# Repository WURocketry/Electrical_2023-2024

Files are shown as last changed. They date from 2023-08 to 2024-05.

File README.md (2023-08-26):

# Electrical
Electrical / Software Development

* Circuit CAD
* Software

### Subteam Folders
Subteams are free to modify their own folder as they like - keep all your subteam related files/articles/figures within that folder.

### Subteam Branches
The "main" Electrical repository is organized into 2 subteam development branches:

* "dev/avionics"
* "dev/payload"
* "dev/airbrakes"

Subteam changes should be pushed and pull requests made only to the respective development subteam branch!

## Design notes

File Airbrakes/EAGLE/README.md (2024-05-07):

# EAGLE IS DEPRECATED

## Use Fusion360 or alternatives

### The archived PACE was moved to the `EAGLE/` folder at the root of the 2023-2024 Electrical repo.

The team is likely using Altium and KiCad for 2025.

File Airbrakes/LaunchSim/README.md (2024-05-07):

Folder for simulation of theoretical airbrake control mechanisms including:
> * Trajectory simulator
> * VLT
> * Actuation control algorithms (PID)

A big yappin folder, courtesy of William (@wurdahl). But really important.

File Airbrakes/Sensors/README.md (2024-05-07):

Folder for sensor tests/example scripts.

Note that these kind of things should be moved to the EE repo in the future, instead of each UFS project having an isolated test area.

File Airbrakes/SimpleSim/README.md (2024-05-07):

A simple python simulation of the vehicle using motor data.

Written and yapped by Patrick (@pjkirby31)

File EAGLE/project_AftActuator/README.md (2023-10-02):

This contains EAGLE project files for the aft servo actuator board

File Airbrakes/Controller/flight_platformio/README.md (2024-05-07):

The home of airbrakes software.

## Root folder Hierarchy

### include/
This folder contains all the header files for every source file. 

A key file is the IMPORTANT_CONFIG.h file containing important configurations (go figure) of ACE software used during flight/development.

### src/
The corresponding definitions/implementations of the header files' classes

### lib/
External 3rd party libraries providing functionality

### test/
Never used. Rip. We should test code, and platformio provides a framework for that.

## Subfolder Hierarchy

### capabilities/
Contains UFS application software layer classes

### components/
Contains UFS component link layer classes

### simulation/
Files for simulating integration test data of the ACE

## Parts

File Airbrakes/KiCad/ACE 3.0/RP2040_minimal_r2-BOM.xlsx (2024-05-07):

RP2040_minimal_r2 BOM
Item | Quantity | Reference | Part | Voltage | Current | Power | Material | Size | Tolerance | Manufacturer | Manuf. Part # | Description | Notes
1 | 3 | C1,C4,C17 | 10u | 16V |  |  | X5R | 0805_2012Metric | 10% | Murata | GRM21BR61C106KE15K | CAP CER 10UF 16V X5R 0805 | Or equivalent
2 | 2 | C2, C3 | 15p | 50V |  |  | C0G | 0402_1005Metric | 5% | Murata | GCM1555C1H150JA16D | CAP CER 15PF 50V C0G/NP0 0402 | Or equivalent
3 | 10 | C5, C6, C7, C9, C11, C12, C13, C14, C15, C16 | 100n | 25V |  |  | X7R | 0402_1005Metric | 10% | Murata | GRM155R71E104KE14J | CAP CER 0.1UF 25V X7R 0402 | Or equivalent
4 | 2 | C8, C10 | 1u | 10V |  |  | X6S | 0402_1005Metric | 10% | Murata | GRM155C81A105KA12D | CAP CER 1UF 10V X6S 0402 | Or equivalent
5 | 1 | J1 | USB_B_Micro |  |  |  |  |  |  | Amphenol | 10103594-0001LF | CONN RCPT USB2.0 MICRO B SMD R/A | Or equivalent
6 | 1 | J2 | 1x2 way header |  |  |  |  |  |  | Samtec | TSW-102-23-T-S | 2.54mm pin header 1x2 | Or equivalent
7 | 2 | J3, J4 | 2x18 way header |  |  |  |  |  |  | Samtec | TSW-118-23-T-D | 2.54mm pin header 2x18 | Or equivalent
8 | 2 | R1, R5 | 1k |  |  | 63mW |  | 0402_1005Metric | 1% | Yageo | RC0402FR-071KP | RES SMD 1K OHM 1% 1/16W 0402 | Or equivalent
9 | 1 | R2 | DNF |  |  |  |  | 0402_1005Metric |  |  |  |  | Do Not Fit
10 | 2 | R3, R4 | 27.4 |  |  | 63mW |  | 0402_1005Metric | 1% | Yageo | RC0402FR-0727R4L | RES SMD 27.4 OHM 1% 1/16W 0402 | Or equivalent
11 | 1 | U1 | NCP1117-3.3 |  |  |  |  | SOT-223-3 |  | ON Semiconductor | NCP1117ST33T3G | IC REG LINEAR 3.3V 1A SOT223
12 | 1 | U2 | W25Q128JVS |  |  |  |  | SOIC-8 |  | Winbond | W25Q128JVSIQ TR | IC FLASH 128M SPI 133MHZ 8SOIC
13 | 1 | U3 | RP2040 |  |  |  |  | QFN56 |  | Raspberry Pi | RP2040
14 | 1 | Y1 | ABM8-272-T3 |  |  |  |  | SMD_3225 |  | Abracon | ABM8-272-T3 | CRYSTAL 12.0000MHZ 3.2x2.5MM SMD

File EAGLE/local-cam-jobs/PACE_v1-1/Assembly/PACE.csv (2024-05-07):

Qty | Value | Device | Package | Parts | Description | AVAILABILITY | BOM | CHECK_PRICES | COMMENT | COPYRIGHT | DESCRIPTION | DIGIKEY_PART_NUMBER_1 | MANUFACTURER | MANUFACTURER_PART_NUMBER | MAXIMUM_PACKAGE_HEIGHT | MF | MFR_NAME | MP | PACKAGE | PARTREV | PRICE | PURCHASE-URL | SNAPEDA_LINK | STANDARD
1 |  | HEADER-1X4ROUND | 1X04_ROUND | JP3 | PIN HEADER
1 |  | HEADER-1X670MIL | 1X06_ROUND_70 | JP2 | PIN HEADER
1 |  | HEADER-1X870MIL | 1X08_ROUND_70 | JP1 | PIN HEADER
1 | 282837-2 | 282837-2 | TE_282837-2 | ACE_ROT3 | TERM BLOCK 5.08MM 2POS SIDE ENTY Check availability | In Stock |  | https://www.snapeda.com/parts/282837-2/TE+Connectivity+AMP+Connectors/view-part/?ref=eda | 282837-2 |  | Terminal Block Connector Wire Receptacle 2 5.08 mm 30-16 AWG Green 13.5 A 250 V | TE Connectivity 282837-2 |  |  |  |  | TE Connectivity |  | 282837-2 | None |  | None | https://www.snapeda.com/api/url_track_click_mouser/?unipart_id=2549980&manufacturer=TE Connectivity&part_name=282837-2&search_term=None | https://www.snapeda.com/parts/282837-2/TE+Connectivity+AMP+Connectors/view-part/?ref=snap
1 | 885012005009 | 885012005009 | CAP_885012005_WRE | C6 |  |  |  |  |  | Copyright (C) 2024 Ultra Librarian. All rights reserved. |  |  |  | 885012005009 |  |  | Wurth Electronics
1 | ABX00042_HEADERS_IO | ABX00042_HEADERS_IO | MODULE_ABX00042_HEADERS | U$10 | Device for Portenta H7 pin headers IO
1 | ADAFRUIT_BNO08X | ADAFRUIT_BNO08X | ADAFRUIT_BNO08X_FOOTPRINT | U$5 | Adafruit BNO08x Device
1 | B03B-PASK-1_(LF)_(SN) | B03B-PASK-1_(LF)_(SN) | CONN_B03B-PASK-1_(LF)_(SN)_JST | SERVOCON |  |  |  |  |  | Copyright (C) 2024 Ultra Librarian. All rights reserved. |  | 455-1833-ND |  | B03B-PASK-1 (LF) (SN) |  |  | JST
3 | CL31B226KPHNNNE | CL31B226KPHNNNE | CAP_CL31_SAM | C2A1, C4, C5 |  |  |  |  |  | Copyright (C) 2024 Ultra Librarian. All rights reserved. |  |  |  | CL31B226KPHNNNE |  |  | Samsung
1 | ERA3AEB6981V | ERA3AEB6981V | RES_ERA3A_0603_PAN | R7 |  |  |  |  |  | Copyright (C) 2024 Ultra Librarian. All rights reserved. |  |  |  | ERA3AEB6981V |  |  | Panasonic
1 | ERJ-3EKF5102V | ERJ-3EKF5102V | RC0603N_PAN | R8 |  |  |  |  |  | Copyright (C) 2024 Ultra Librarian. All rights reserved. |  |  |  | ERJ-3EKF5102V |  |  | Panasonic
1 | ERJ3EKF51R0V | ERJ3EKF51R0V | RES_ERJ3EKF51R0V | R1 |  |  |  |  |  |  |  |  | Panasonic |  | 0.45 mm |  |  |  |  | 3/1/2020 |  |  |  | Manufacturer Recommendations
2 | MOUNTINGHOLE2.0 | MOUNTINGHOLE2.0 | MOUNTINGHOLE_2.0_PLATED | U$1, U$3 | Mounting Hole |  | EXCLUDE
1 | MPM3630GQV-P | MPM3630GQV-P | QFN3P0X5P0X1P6_MPM3630_MNP | U2 |  |  |  |  |  | Copyright (C) 2024 Ultra Librarian. All rights reserved. |  |  |  | MPM3630GQV-P |  |  | Monolithic Power Systems
1 | PTH | I2C_STANDARD_NO_SILK | 1X04_NO_SILK | J3 | SparkFun I2C Standard Pinout Header
1 | RC1005F103CS | RC1005F103CS | RES_1005_SAM | R3 |  |  |  |  |  | Copyright (C) 2024 Ultra Librarian. All rights reserved. |  |  |  | RC1005F103CS |  |  | Samsung
1 | RM04F1003CT | RM04F1003CT | RES_RM04_CCE | R6 |  |  |  |  |  | Copyright (C) 2024 Ultra Librarian. All rights reserved. |  |  |  | RM04F1003CT |  |  | Cal-Chip Electronics
4 | USB-C | USB-C | USB-C | CAM1, CAM2, CAM3, CAM4 | Check availability | Not in stock |  | https://www.snapeda.com/parts/USB-C/Adam+Tech/view-part/?ref=eda |  |  | USB-C (USB TYPE-C) USB 3.2 Gen 2 (USB 3.1 Gen 2, Superspeed + (USB 3.1)) Receptacle Connector 24 Position Surface Mount, Through Hole |  |  |  |  | Adam Technologies |  | USB-C | None |  | None |  | https://www.snapeda.com/parts/USB-C/Adam+Tech/view-part/?ref=snap
1 | XT30PW-F | XT30PW-F | AMASS_XT30PW-F | BATT_TERM | Check availability | Not in stock |  | https://www.snapeda.com/parts/XT30PW-F/AMASS/view-part/?ref=eda |  |  | Socket | DC supply | XT30 | female | PIN: 2 | on PCBs | THT | yellow | 15A |  |  |  |  | amass

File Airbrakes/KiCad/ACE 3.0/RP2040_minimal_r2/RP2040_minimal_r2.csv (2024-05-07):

Id | Designator | Footprint | Quantity | Designation | Supplier and ref
1 | U6 | BGA9_BMM350_BOS | 1 | BMM350
2 | U5 | QFN10_BMP581_BOS | 1 | BMP581
3 | C24 | CAPC2012X55N | 1 | 2.2u
4 | C23,C22,C21,C20,C19,C18,C13,C5,C9,C12,C14,C7,C11,C16,C6,C15 | C_0402_1005Metric | 16 | 100n
5 | U4 | PQFN50P450X300X100-16N | 1 | BMI088
6 | C4,C1,C17 | C_0805_2012Metric | 3 | 10u
7 | J1 | USB_Micro-B_Amphenol_10103594-0001LF_Horizontal_modified | 1 | USB_B_Micro
8 | J2 | PinHeader_1x02_P2.54mm_Vertical | 1 | Conn_01x02
9 | J3,J4 | PinHeader_2x18_P2.54mm_Vertical | 2 | Conn_02x18_Odd_Even
10 | C10,C8 | C_0402_1005Metric | 2 | 1u
11 | R2 | R_0402_1005Metric | 1 | DNF
12 | U1 | SOT-223-3_TabPin2 | 1 | NCP1117-3.3_SOT223
13 | U2 | SOIC-8_5.23x5.23mm_P1.27mm | 1 | W25Q128JVS
14 | R1,R5 | R_0402_1005Metric | 2 | 1k
15 | R3,R4 | R_0402_1005Metric | 2 | 27
16 | U3 | RP2040-QFN-56 | 1 | RP2040
17 | H2,H3,H1,H4 | MountingHole_2.7mm_M2.5 | 4 | MountingHole
18 | C2,C3 | C_0402_1005Metric | 2 | 15p
19 | Y1 | Crystal_SMD_3225-4Pin_3.2x2.5mm | 1 | ABM8-272-T3

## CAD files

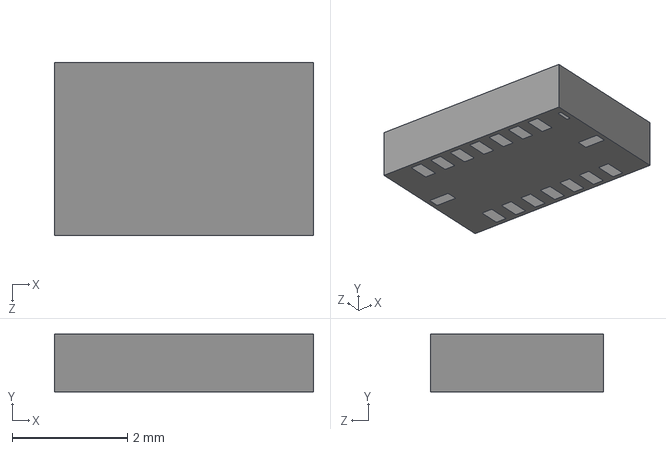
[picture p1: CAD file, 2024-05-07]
Airbrakes/KiCad/ACE 3.0/RP2040_minimal_r2/local-libraries/BMI088/BMI088.step
4.50 x 1.00 x 3.00 mm

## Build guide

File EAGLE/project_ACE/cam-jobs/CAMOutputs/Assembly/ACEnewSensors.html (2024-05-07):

Partlist exported from C:/Users/Bylue/Desktop/WUSTL/WURocketry/2023-2024/repositories/Electrical/Airbrakes/EAGLE/project_ACE/ACEnewSensors.sch at 2/14/2024 10:09 PM

Part | Value | Device | Package | Description | AVAILABILITY | BOM | CHECK_PRICES | COMMENT | COPYRIGHT | DESCRIPTION | DIGIKEY_PART_NUMBER_1 | MANUFACTURER | MANUFACTURER_PART_NUMBER | MAXIMUM_PACKAGE_HEIGHT | MF | MFR_NAME | MP | PACKAGE | PARTREV | PRICE | PURCHASE-URL | SNAPEDA_LINK | STANDARD
ACE_ROT3 | 282837-2 | 282837-2 | TE_282837-2 | TERM BLOCK 5.08MM 2POS SIDE ENTY Check availability | In Stock | | https://www.snapeda.com/parts/282837-2/TE+Connectivity+AMP+Connectors/view-part/?ref=eda | 282837-2 | | Terminal Block Connector Wire Receptacle 2 5.08 mm 30-16 AWG Green 13.5 A 250 V | TE Connectivity 282837-2 | | | | | TE Connectivity | | 282837-2 | None | | None | https://www.snapeda.com/api/url_track_click_mouser/?unipart_id=2549980&manufacturer=TE Connectivity&part_name=282837-2&search_term=None | https://www.snapeda.com/parts/282837-2/TE+Connectivity+AMP+Connectors/view-part/?ref=snap
BATT_TERM | XT30PW-F | XT30PW-F | AMASS_XT30PW-F | Check availability | Not in stock | | https://www.snapeda.com/parts/XT30PW-F/AMASS/view-part/?ref=eda | | | Socket | DC supply | XT30 | female | PIN: 2 | on PCBs | THT | yellow | 15A | | | | | amass
C2A1 | CL31B226KPHNNNE | CL31B226KPHNNNE | CAP_CL31_SAM | | | | | | Copyright (C) 2024 Ultra Librarian. All rights reserved. | | | | CL31B226KPHNNNE | | | Samsung
C4 | CL31B226KPHNNNE | CL31B226KPHNNNE | CAP_CL31_SAM | | | | | | Copyright (C) 2024 Ultra Librarian. All rights reserved. | | | | CL31B226KPHNNNE | | | Samsung
C5 | CL31B226KPHNNNE | CL31B226KPHNNNE | CAP_CL31_SAM | | | | | | Copyright (C) 2024 Ultra Librarian. All rights reserved. | | | | CL31B226KPHNNNE | | | Samsung
C6 | 885012005009 | 885012005009 | CAP_885012005_WRE | | | | | | Copyright (C) 2024 Ultra Librarian. All rights reserved. | | | | 885012005009 | | | Wurth Electronics
CAM1 | 10118194-0001LF | 10118194-0001LF | AMPHENOL_10118194-0001LF | Check availability | In Stock | | https://www.snapeda.com/parts/10118194-0001LF/Amphenol+FCI/view-part/?ref=eda | | | Micro USB, Input Output Connectors, B TYPE RECEPTACLE with flange | | | | | Amphenol ICC | | 10118194-0001LF | None | | None | https://www.snapeda.com/api/url_track_click_mouser/?unipart_id=47625&manufacturer=Amphenol ICC&part_name=10118194-0001LF&search_term=None | https://www.snapeda.com/parts/10118194-0001LF/Amphenol+FCI/view-part/?ref=snap
CAM2 | 10118194-0001LF | 10118194-0001LF | AMPHENOL_10118194-0001LF | Check availability | In Stock | | https://www.snapeda.com/parts/10118194-0001LF/Amphenol+FCI/view-part/?ref=eda | | | Micro USB, Input Output Connectors, B TYPE RECEPTACLE with flange | | | | | Amphenol ICC | | 10118194-0001LF | None | | None | https://www.snapeda.com/api/url_track_click_mouser/?unipart_id=47625&manufacturer=Amphenol ICC&part_name=10118194-0001LF&search_term=None | https://www.snapeda.com/parts/10118194-0001LF/Amphenol+FCI/view-part/?ref=snap
CAM3 | 10118194-0001LF | 10118194-0001LF | AMPHENOL_10118194-0001LF | Check availability | In Stock | | https://www.snapeda.com/parts/10118194-0001LF/Amphenol+FCI/view-part/?ref=eda | | | Micro USB, Input Output Connectors, B TYPE RECEPTACLE with flange | | | | | Amphenol ICC | | 10118194-0001LF | None | | None | https://www.snapeda.com/api/url_track_click_mouser/?unipart_id=47625&manufacturer=Amphenol ICC&part_name=10118194-0001LF&search_term=None | https://www.snapeda.com/parts/10118194-0001LF/Amphenol+FCI/view-part/?ref=snap
CAM4 | 10118194-0001LF | 10118194-0001LF | AMPHENOL_10118194-0001LF | Check availability | In Stock | | https://www.snapeda.com/parts/10118194-0001LF/Amphenol+FCI/view-part/?ref=eda | | | Micro USB, Input Output Connectors, B TYPE RECEPTACLE with flange | | | | | Amphenol ICC | | 10118194-0001LF | None | | None | https://www.snapeda.com/api/url_track_click_mouser/?unipart_id=47625&manufacturer=Amphenol ICC&part_name=10118194-0001LF&search_term=None | https://www.snapeda.com/parts/10118194-0001LF/Amphenol+FCI/view-part/?ref=snap
J3 | PTH | I2C_STANDARD_NO_SILK | 1X04_NO_SILK | SparkFun I2C Standard Pinout Header
JP1 | | HEADER-1X870MIL | 1X08_ROUND_70 | PIN HEADER
JP2 | | HEADER-1X670MIL | 1X06_ROUND_70 | PIN HEADER
JP3 | | HEADER-1X4ROUND | 1X04_ROUND | PIN HEADER
R1 | ERJ3EKF51R0V | ERJ3EKF51R0V | RES_ERJ3EKF51R0V | | | | | | | | | Panasonic | | 0.45 mm | | | | | 3/1/2020 | | | | Manufacturer Recommendations
R3 | RC1005F103CS | RC1005F103CS | RES_1005_SAM | | | | | | Copyright (C) 2024 Ultra Librarian. All rights reserved. | | | | RC1005F103CS | | | Samsung
R6 | RM04F1003CT | RM04F1003CT | RES_RM04_CCE | | | | | | Copyright (C) 2024 Ultra Librarian. All rights reserved. | | | | RM04F1003CT | | | Cal-Chip Electronics
R7 | ERA3AEB6981V | ERA3AEB6981V | RES_ERA3A_0603_PAN | | | | | | Copyright (C) 2024 Ultra Librarian. All rights reserved. | | | | ERA3AEB6981V | | | Panasonic
R8 | ERJ-3EKF5102V | ERJ-3EKF5102V | RC0603N_PAN | | | | | | Copyright (C) 2024 Ultra Librarian. All rights reserved. | | | | ERJ-3EKF5102V | | | Panasonic
SERVOCON | B03B-PASK-1_(LF)_(SN) | B03B-PASK-1_(LF)_(SN) | CONN_B03B-PASK-1_(LF)_(SN)_JST | | | | | | Copyright (C) 2024 Ultra Librarian. All rights reserved. | | 455-1833-ND | | B03B-PASK-1 (LF) (SN) | | | JST
U$1 | MOUNTINGHOLE2.0 | MOUNTINGHOLE2.0 | MOUNTINGHOLE_2.0_PLATED | Mounting Hole | | EXCLUDE
U$3 | MOUNTINGHOLE2.0 | MOUNTINGHOLE2.0 | MOUNTINGHOLE_2.0_PLATED | Mounting Hole | | EXCLUDE
U$5 | ADAFRUIT_BNO08X | ADAFRUIT_BNO08X | ADAFRUIT_BNO08X_FOOTPRINT | Adafruit BNO08x Device
U$10 | ABX00042_HEADERS_IO | ABX00042_HEADERS_IO | MODULE_ABX00042_HEADERS | Device for Portenta H7 pin headers IO
U2 | MPM3630GQV-P | MPM3630GQV-P | QFN3P0X5P0X1P6_MPM3630_MNP | | | | | | Copyright (C) 2024 Ultra Librarian. All rights reserved. | | | | MPM3630GQV-P | | | Monolithic Power Systems

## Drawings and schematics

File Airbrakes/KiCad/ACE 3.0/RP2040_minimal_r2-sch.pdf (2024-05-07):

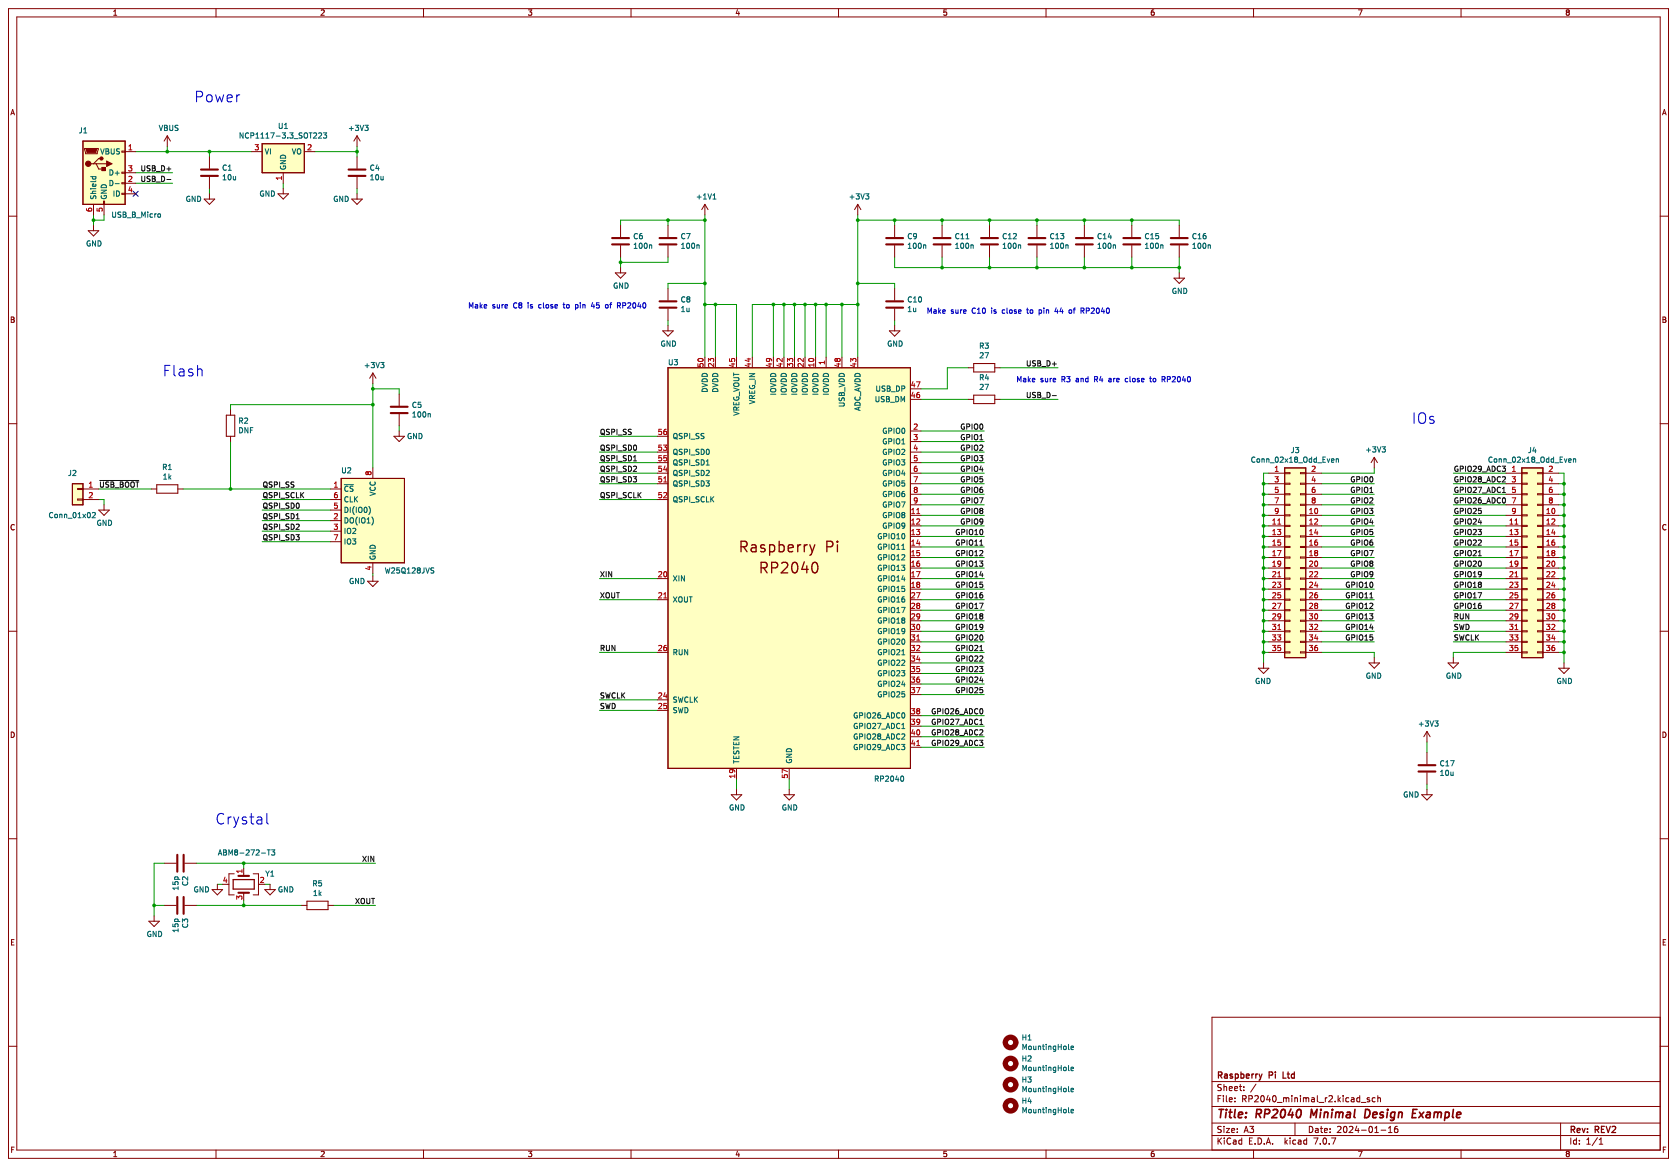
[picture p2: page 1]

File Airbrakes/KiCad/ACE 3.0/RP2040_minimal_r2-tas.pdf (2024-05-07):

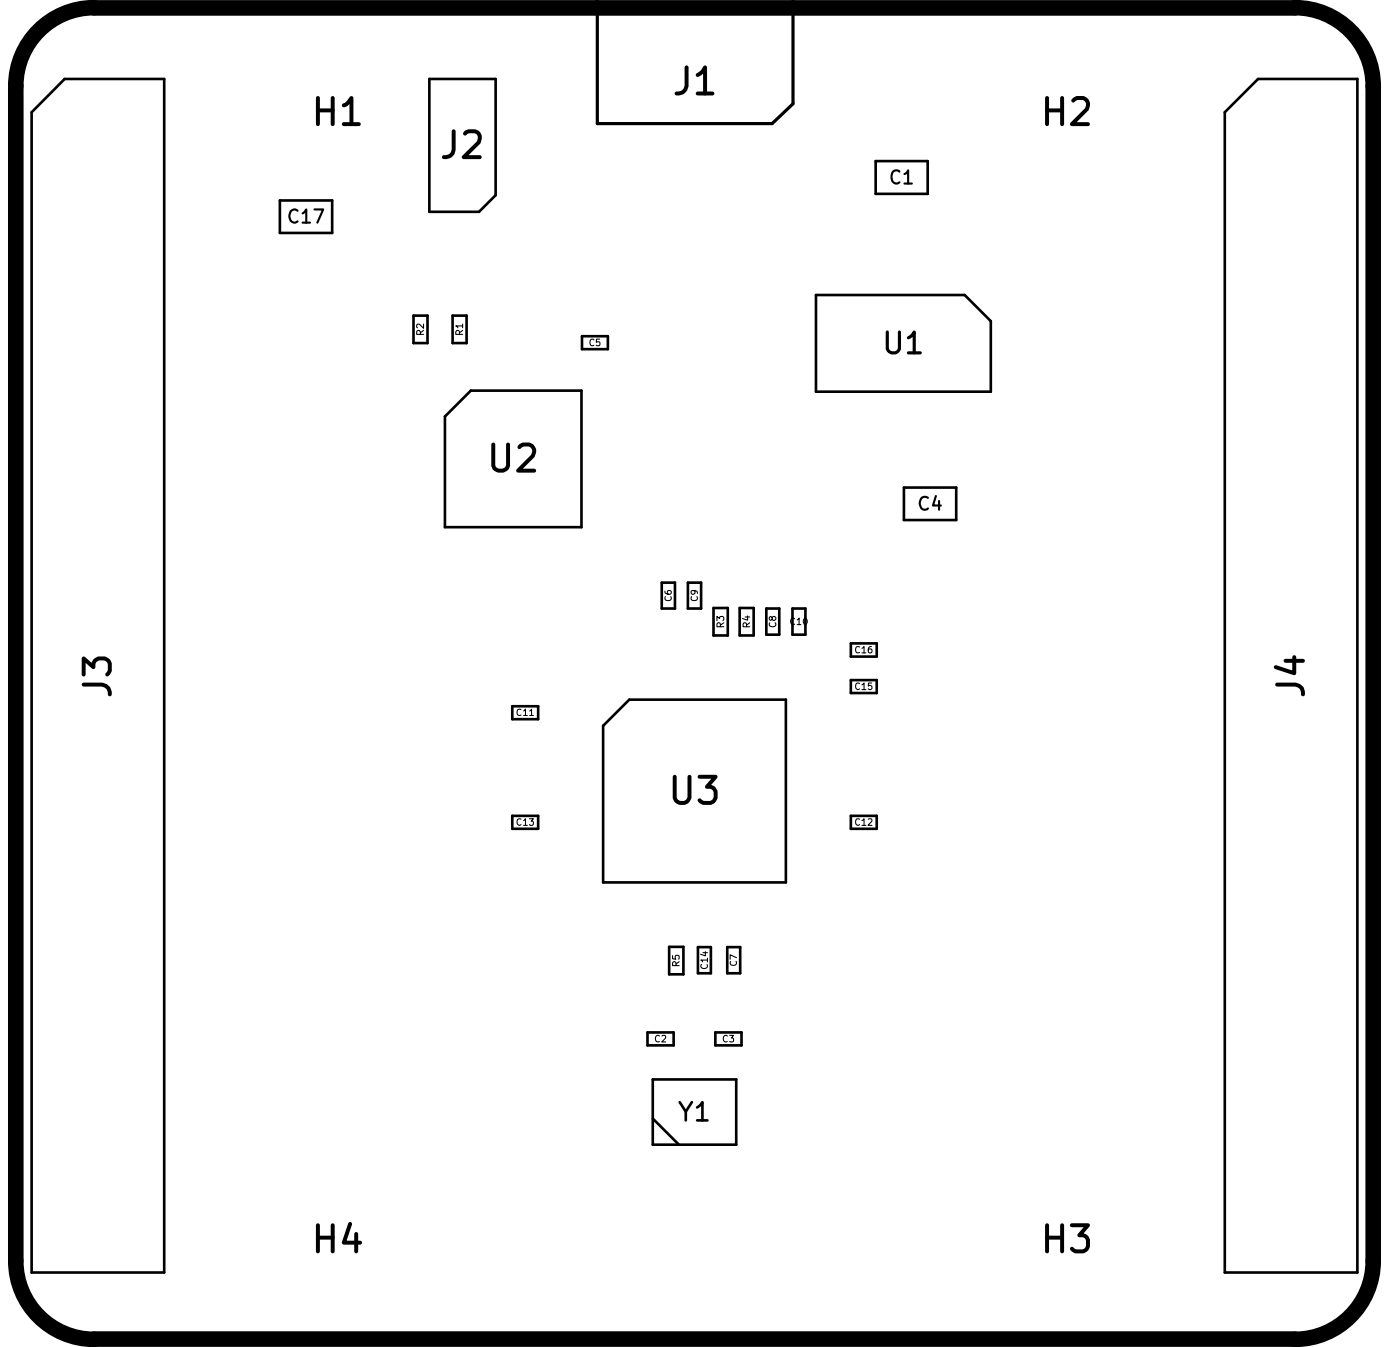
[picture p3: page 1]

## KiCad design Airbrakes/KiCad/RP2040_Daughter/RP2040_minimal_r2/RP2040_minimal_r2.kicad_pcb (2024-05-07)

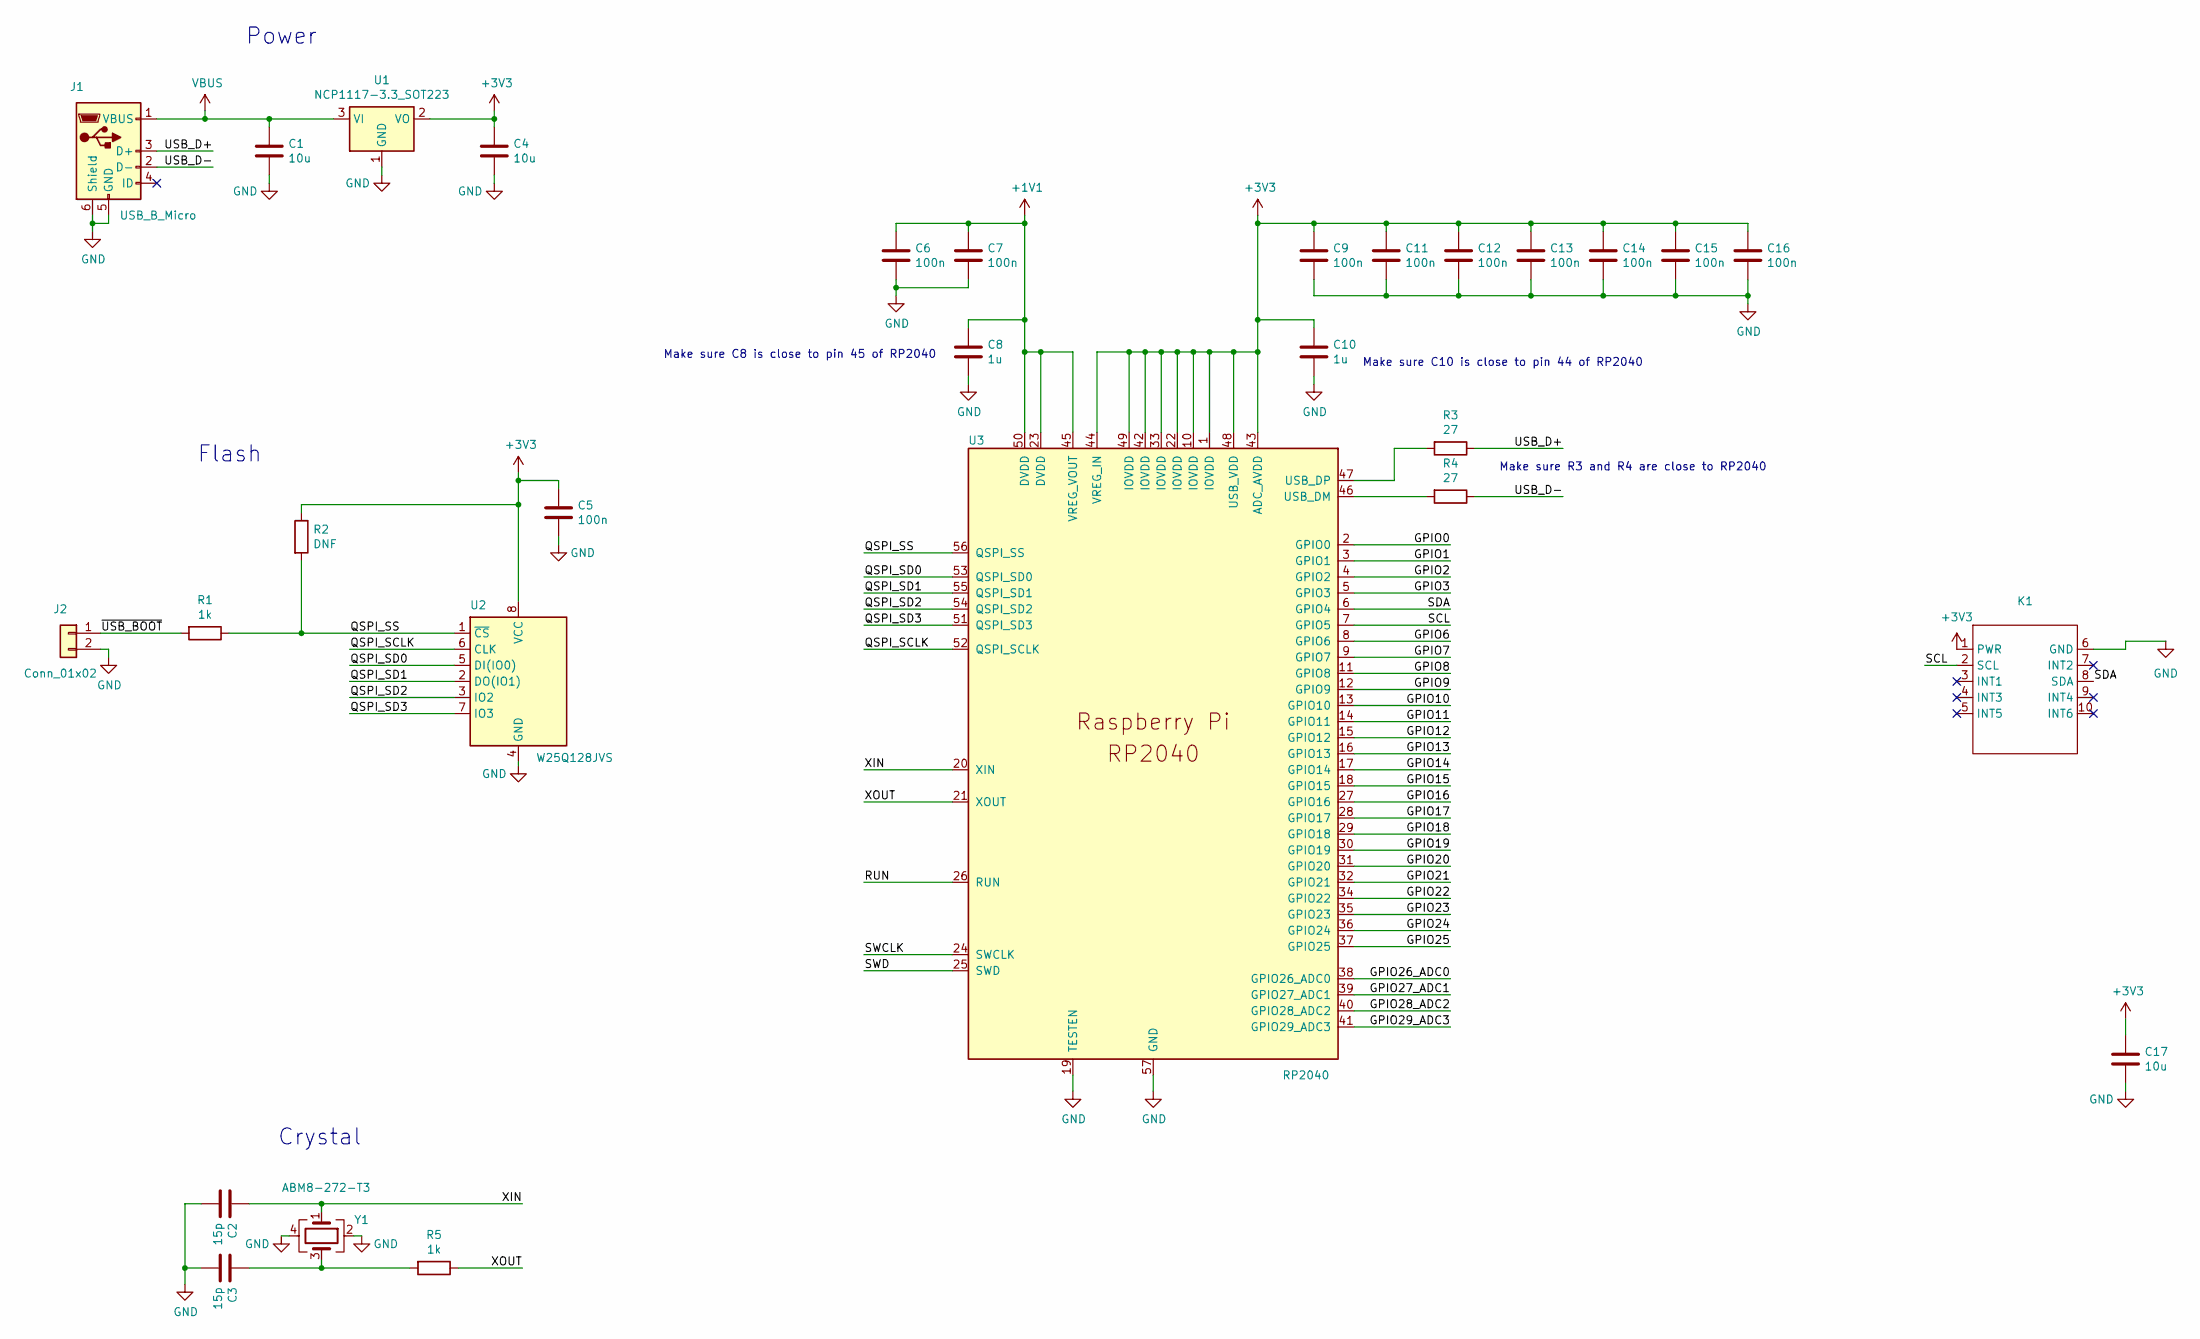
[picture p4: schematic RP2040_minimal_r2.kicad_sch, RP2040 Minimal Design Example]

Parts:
C1, C4, C17: 10u; C_0805_2012Metric
C2, C3: 15p; C_0402_1005Metric
C5, C6, C7, C9, C11, C12, C13, C14, C15, C16: 100n; C_0402_1005Metric
C8, C10: 1u; C_0402_1005Metric
J1: USB_B_Micro; USB_Micro-B_Amphenol_10103594-0001LF_Horizontal_modified
J2: Conn_01x02; PinHeader_1x02_P2.54mm_Vertical
K1: 12_Pin_Edge_Connector
R1, R5: 1k; R_0402_1005Metric
R2: DNF; R_0402_1005Metric
R3, R4: 27; R_0402_1005Metric
U1: NCP1117-3.3_SOT223; SOT-223-3_TabPin2
U2: W25Q128JVS; SOIC-8_5.23x5.23mm_P1.27mm
U3: RP2040; RP2040-QFN-56
Y1: ABM8-272-T3; Crystal_SMD_3225-4Pin_3.2x2.5mm

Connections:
+1V1: C6.1, C7.1, C8.1, U3.23 (DVDD), U3.45 (VREG_VOUT), U3.50 (DVDD)
+3V3: C4.1, C5.1, C9.1, C10.1, C11.1, C12.1, C13.1, C14.1, C15.1, C16.1, C17.1, K1.1 (PWR), R2.1, U1.2 (VO), U2.8 (VCC), U3.1 (IOVDD), U3.10 (IOVDD), U3.22 (IOVDD), U3.33 (IOVDD), U3.42 (IOVDD), U3.43 (ADC_AVDD), U3.44 (VREG_IN), U3.48 (USB_VDD), U3.49 (IOVDD)
/GPIO0: U3.2 (GPIO0)
/GPIO1: U3.3 (GPIO1)
/GPIO2: U3.4 (GPIO2)
/GPIO3: U3.5 (GPIO3)
/GPIO6: U3.8 (GPIO6)
/GPIO7: U3.9 (GPIO7)
/GPIO8: U3.11 (GPIO8)
/GPIO9: U3.12 (GPIO9)
/GPIO10: U3.13 (GPIO10)
/GPIO11: U3.14 (GPIO11)
/GPIO12: U3.15 (GPIO12)
/GPIO13: U3.16 (GPIO13)
/GPIO14: U3.17 (GPIO14)
/GPIO15: U3.18 (GPIO15)
/GPIO16: U3.27 (GPIO16)
/GPIO17: U3.28 (GPIO17)
/GPIO18: U3.29 (GPIO18)
/GPIO19: U3.30 (GPIO19)
/GPIO20: U3.31 (GPIO20)
/GPIO21: U3.32 (GPIO21)
/GPIO22: U3.34 (GPIO22)
/GPIO23: U3.35 (GPIO23)
/GPIO24: U3.36 (GPIO24)
/GPIO25: U3.37 (GPIO25)
/GPIO26_ADC0: U3.38 (GPIO26_ADC0)
/GPIO27_ADC1: U3.39 (GPIO27_ADC1)
/GPIO28_ADC2: U3.40 (GPIO28_ADC2)
/GPIO29_ADC3: U3.41 (GPIO29_ADC3)
/QSPI_SCLK: U2.6 (CLK), U3.52 (QSPI_SCLK)
/QSPI_SD0: U2.5 (DI(IO0)), U3.53 (QSPI_SD0)
/QSPI_SD1: U2.2 (DO(IO1)), U3.55 (QSPI_SD1)
/QSPI_SD2: U2.3 (IO2), U3.54 (QSPI_SD2)
/QSPI_SD3: U2.7 (IO3), U3.51 (QSPI_SD3)
/QSPI_SS: R1.1, R2.2, U2.1 (~CS), U3.56 (QSPI_SS)
/RUN: U3.26 (RUN)
/SCL: K1.2 (SCL), U3.7 (GPIO5)
/SDA: K1.8 (SDA), U3.6 (GPIO4)
/SWCLK: U3.24 (SWCLK)
/SWD: U3.25 (SWD)
/USB_D+: J1.3 (D+), R3.1
/USB_D-: J1.2 (D-), R4.1
/XIN: C2.1, U3.20 (XIN), Y1.1
/XOUT: R5.1, U3.21 (XOUT)
/~USB_BOOT: J2.1, R1.2
GND: C1.2, C2.2, C3.2, C4.2, C5.2, C6.2, C7.2, C8.2, C9.2, C10.2, C11.2, C12.2, C13.2, C14.2, C15.2, C16.2, C17.2, J1.5 (GND), J1.6 (Shield), J2.2, K1.6 (GND), U1.1 (GND), U2.4 (GND), U3.19 (TESTEN), U3.57 (GND), Y1.2, Y1.4
unnamed: C3.1, R5.2, Y1.3
unnamed: R4.2, U3.46 (USB_DM)
unnamed: R3.2, U3.47 (USB_DP)
VBUS: C1.1, J1.1 (VBUS), U1.3 (VI)

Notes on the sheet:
Power
Crystal
Make sure C8 is close to pin 45 of RP2040
Make sure C10 is close to pin 44 of RP2040
Make sure R3 and R4 are close to RP2040
Flash

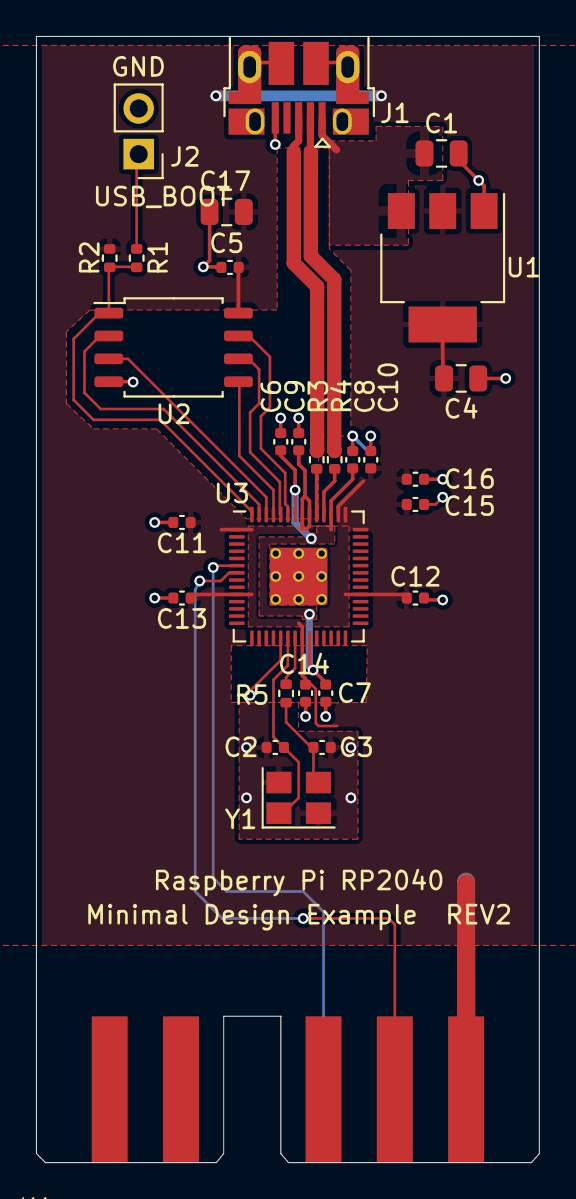
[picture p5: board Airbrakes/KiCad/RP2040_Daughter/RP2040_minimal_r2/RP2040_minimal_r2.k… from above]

Board: 2 copper layers, 27.9 x 62.6 mm, 29 parts (0 on the bottom side), 20 nets.

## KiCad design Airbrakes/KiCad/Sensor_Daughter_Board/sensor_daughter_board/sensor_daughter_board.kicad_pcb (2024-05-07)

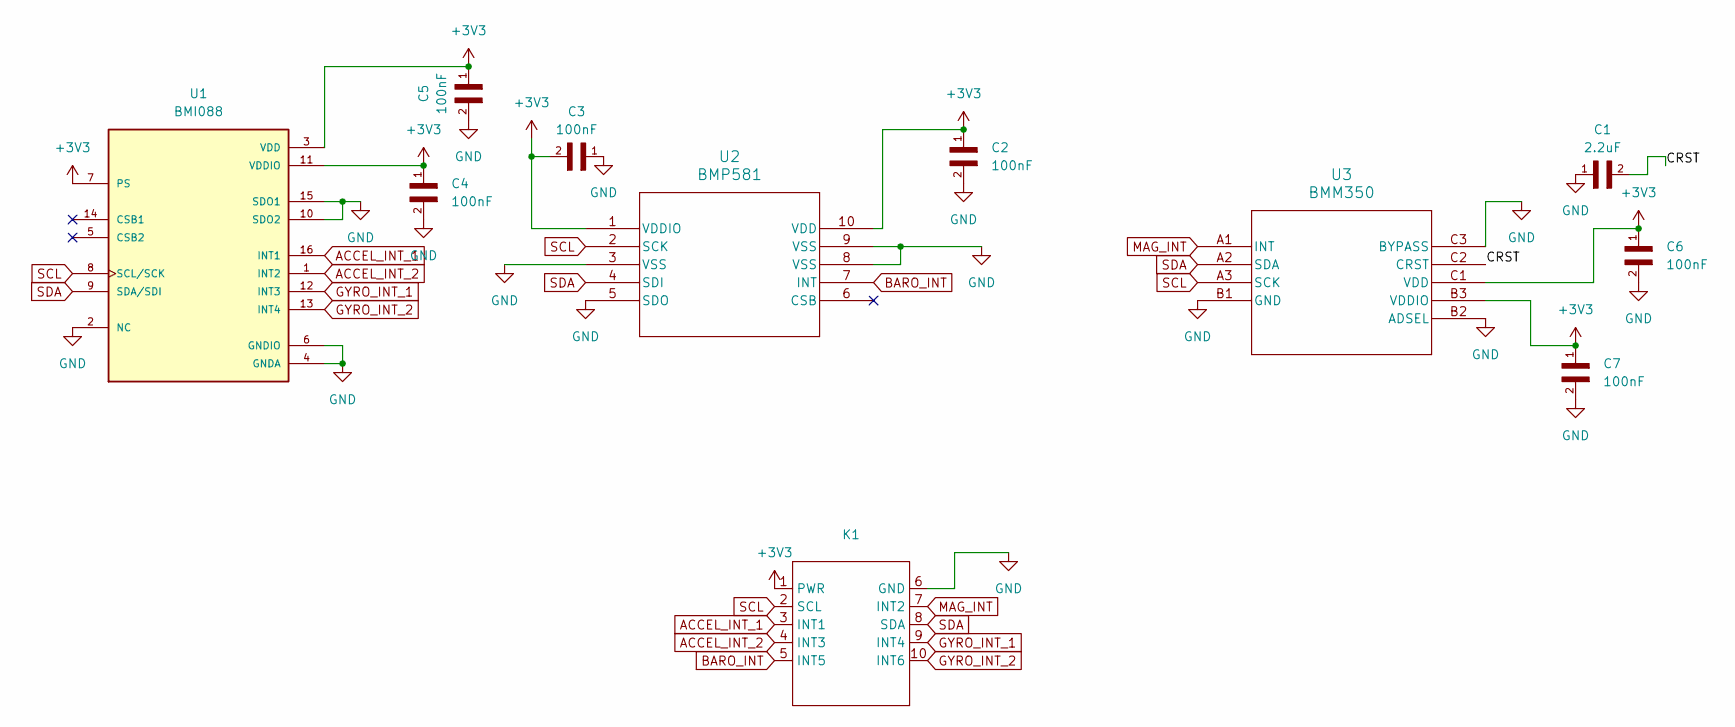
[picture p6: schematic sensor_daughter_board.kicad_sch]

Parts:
C1: 2.2uF; CAPC2012X55N
C2, C3, C4, C5, C6, C7: 100nF; CAPC1005X55N
K1: 12_Pin_Edge_Connector
U1: BMI088; PQFN50P450X300X100-16N
U2: BMP581; QFN10_BMP581_BOS
U3: BMM350; BGA9_BMM350_BOS

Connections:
+3V3: C2.1, C3.2, C4.1, C5.1, C6.1, C7.1, K1.1 (PWR), U1.3 (VDD), U1.7 (PS), U1.11 (VDDIO), U2.1 (VDDIO), U2.10 (VDD), U3.B3 (VDDIO), U3.C1 (VDD)
/CRST: C1.2, U3.C2 (CRST)
ACCEL_INT_1: K1.3 (INT1), U1.16 (INT1)
ACCEL_INT_2: K1.4 (INT3), U1.1 (INT2)
BARO_INT: K1.5 (INT5), U2.7 (INT)
GND: C1.1, C2.2, C3.1, C4.2, C5.2, C6.2, C7.2, K1.6 (GND), U1.2 (NC), U1.4 (GNDA), U1.6 (GNDIO), U1.10 (SDO2), U1.15 (SDO1), U2.3 (VSS), U2.5 (SDO), U2.8 (VSS), U2.9 (VSS), U3.B1 (GND), U3.B2 (ADSEL), U3.C3 (BYPASS)
GYRO_INT_1: K1.9 (INT4), U1.12 (INT3)
GYRO_INT_2: K1.10 (INT6), U1.13 (INT4)
MAG_INT: K1.7 (INT2), U3.A1 (INT)
SCL: K1.2 (SCL), U1.8 (SCL/SCK), U2.2 (SCK), U3.A3 (SCK)
SDA: K1.8 (SDA), U1.9 (SDA/SDI), U2.4 (SDI), U3.A2 (SDA)

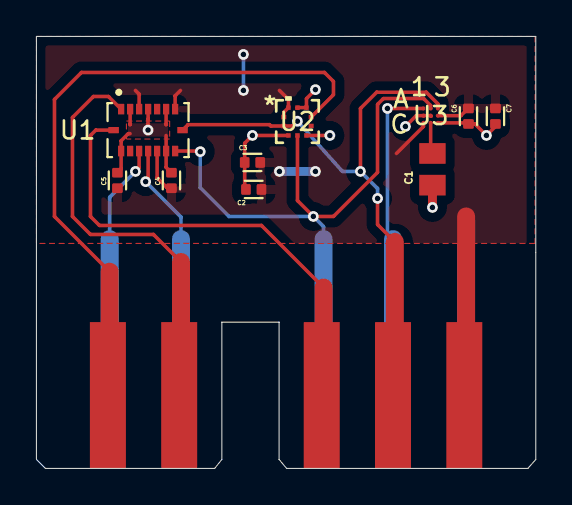
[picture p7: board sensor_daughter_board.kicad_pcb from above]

Board: 2 copper layers, 27.7 x 24.0 mm, 11 parts (0 on the bottom side), 11 nets.

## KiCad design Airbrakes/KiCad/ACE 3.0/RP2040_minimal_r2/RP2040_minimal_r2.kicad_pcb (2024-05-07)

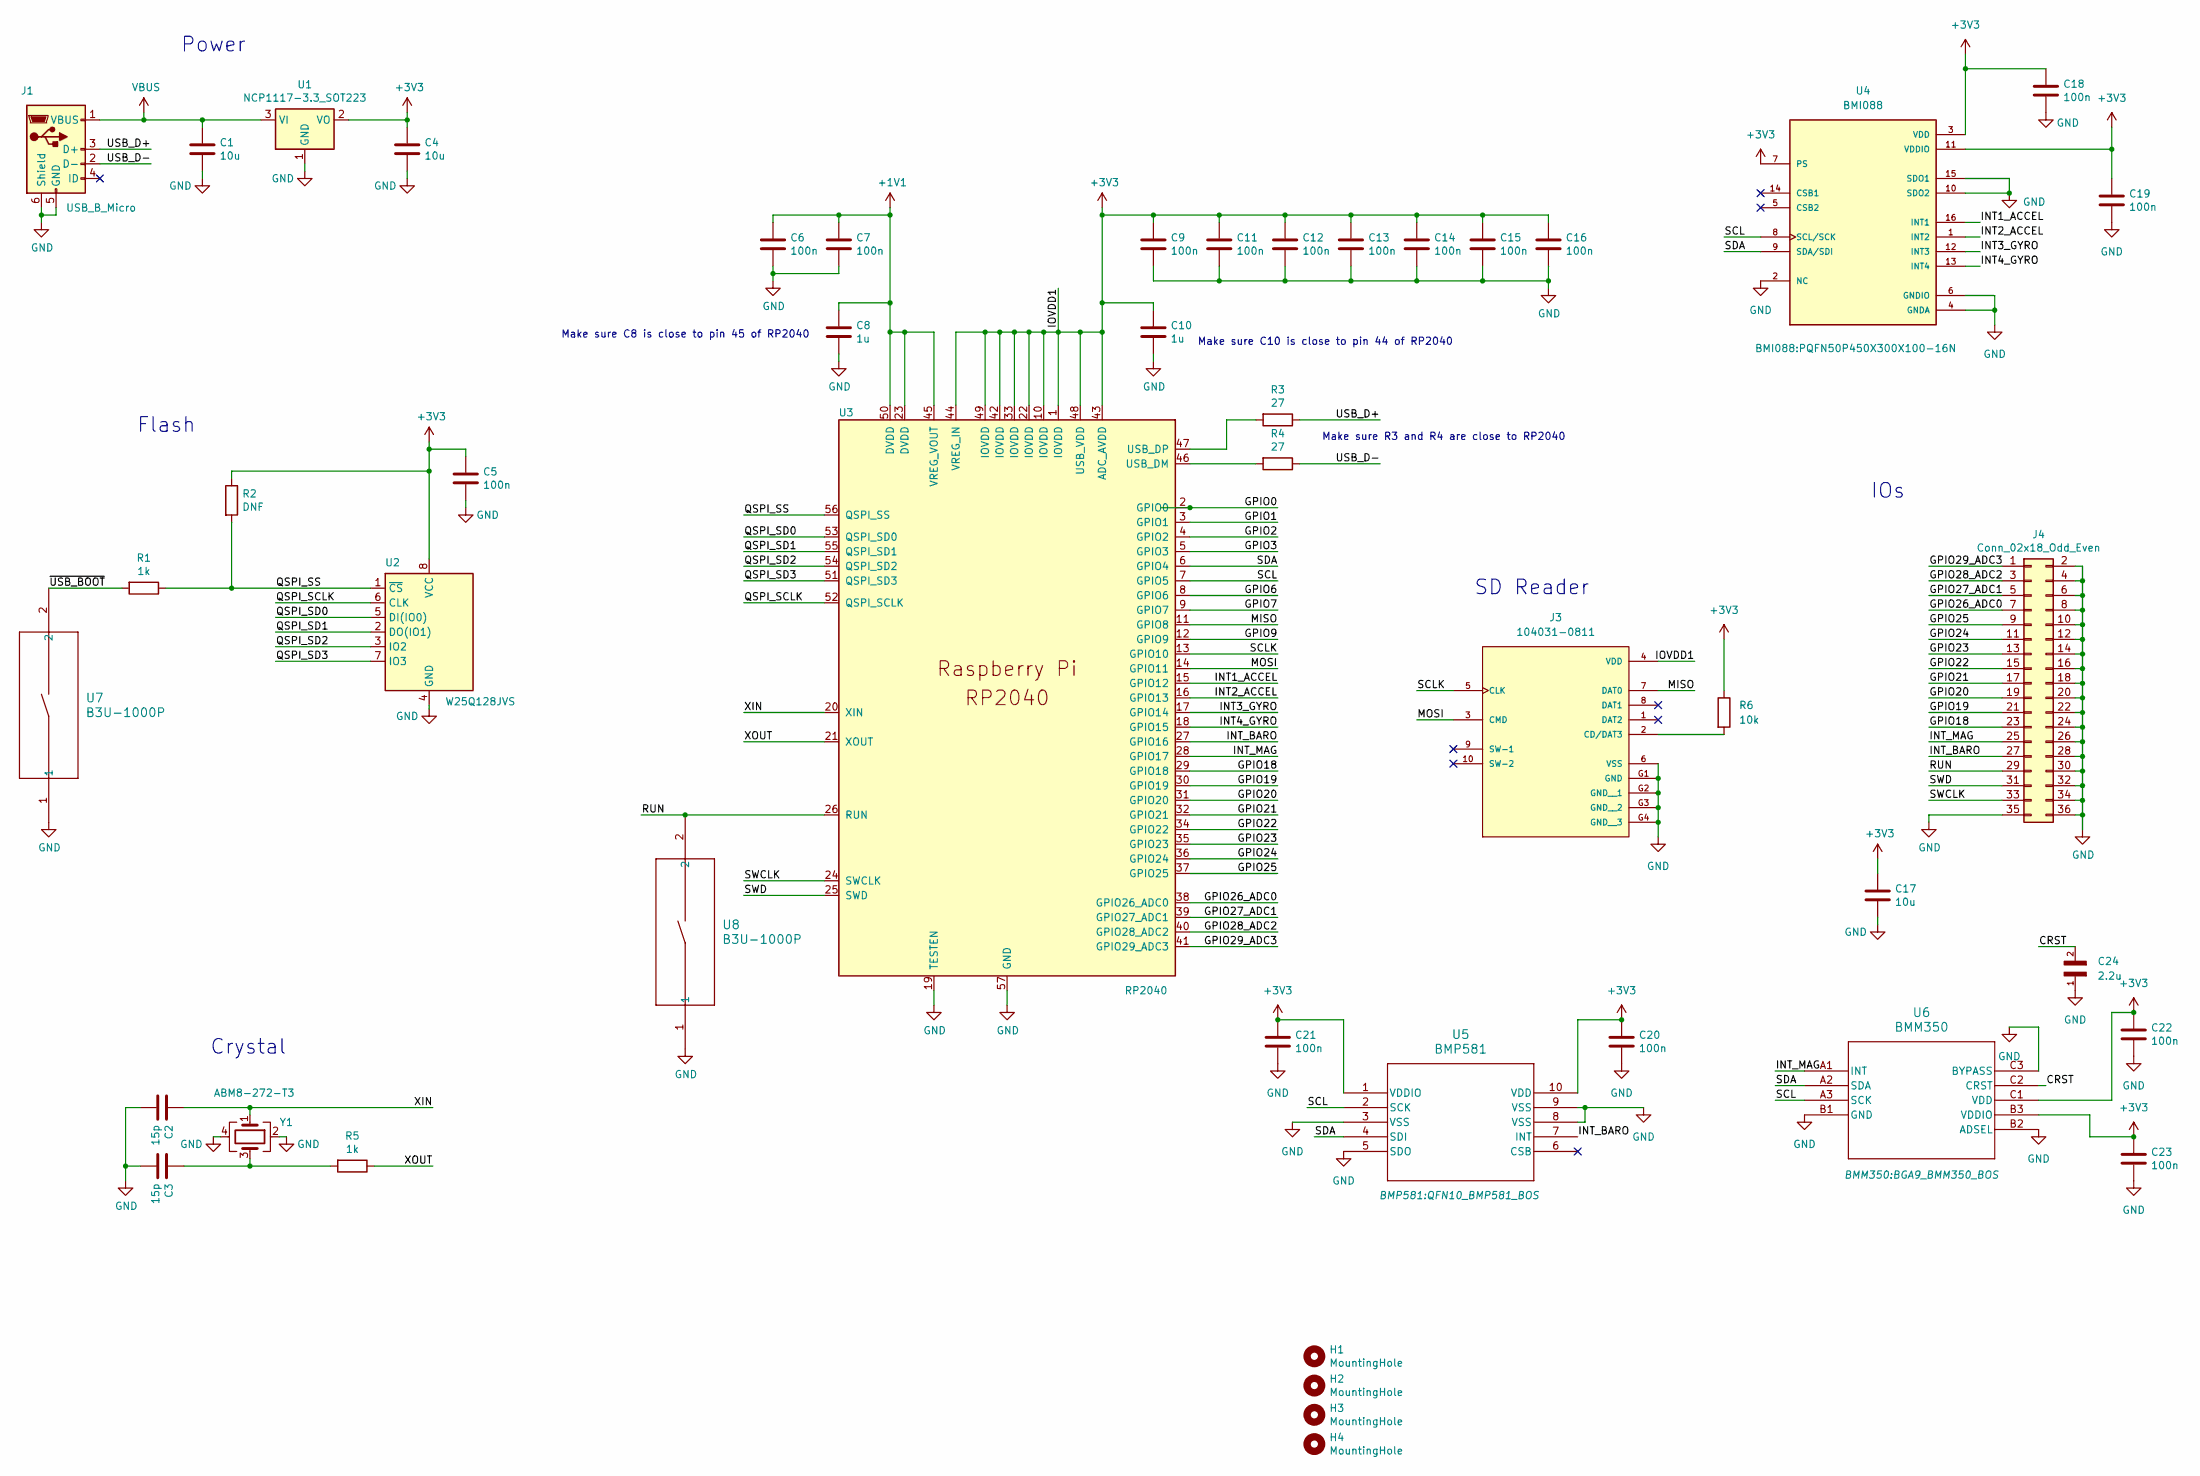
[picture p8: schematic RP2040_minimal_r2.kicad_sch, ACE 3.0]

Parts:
C1, C4, C17: 10u; C_0805_2012Metric
C2, C3: 15p; C_0402_1005Metric
C5, C6, C7, C9, C11, C12, C13, C14, C15, C16, C18, C19, C20, C21, C22, C23: 100n; C_0402_1005Metric
C8, C10: 1u; C_0402_1005Metric
C24: 2.2u; CAPC2012X55N
H1, H2, H3, H4: MountingHole; MountingHole_2.7mm_M2.5
J1: USB_B_Micro; USB_Micro-B_Amphenol_10103594-0001LF_Horizontal_modified
J3: 104031-0811; MOLEX_104031-0811; PARTREV B2
J4: Conn_02x18_Odd_Even; PinHeader_2x18_P2.54mm_Vertical
R1, R5: 1k; R_0402_1005Metric
R2: DNF; R_0402_1005Metric
R3, R4: 27; R_0402_1005Metric
R6: 10k; R_0402_1005Metric
U1: NCP1117-3.3_SOT223; SOT-223-3_TabPin2
U2: W25Q128JVS; SOIC-8_5.23x5.23mm_P1.27mm
U3: RP2040; RP2040-QFN-56
U4: BMI088; PQFN50P450X300X100-16N
U5: BMP581; QFN10_BMP581_BOS
U6: BMM350; BGA9_BMM350_BOS
U7, U8: B3U-1000P; SW_SPST_B3U-1000P
Y1: ABM8-272-T3; Crystal_SMD_3225-4Pin_3.2x2.5mm

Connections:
+1V1: C6.1, C7.1, C8.1, U3.23 (DVDD), U3.45 (VREG_VOUT), U3.50 (DVDD)
+3V3: C4.1, C5.1, C9.1, C10.1, C11.1, C12.1, C13.1, C14.1, C15.1, C16.1, C17.1, C18.1, C19.1, C20.1, C21.1, C22.1, C23.1, J3.4 (VDD), R2.1, R6.1, U1.2 (VO), U2.8 (VCC), U3.1 (IOVDD), U3.10 (IOVDD), U3.22 (IOVDD), U3.33 (IOVDD), U3.42 (IOVDD), U3.43 (ADC_AVDD), U3.44 (VREG_IN), U3.48 (USB_VDD), U3.49 (IOVDD), U4.3 (VDD), U4.7 (PS), U4.11 (VDDIO), U5.1 (VDDIO), U5.10 (VDD), U6.B3 (VDDIO), U6.C1 (VDD)
/CRST: C24.2, U6.C2 (CRST)
/GPIO0: U3.2 (GPIO0)
/GPIO1: U3.3 (GPIO1)
/GPIO2: U3.4 (GPIO2)
/GPIO3: U3.5 (GPIO3)
/GPIO6: U3.8 (GPIO6)
/GPIO7: U3.9 (GPIO7)
/GPIO9: U3.12 (GPIO9)
/GPIO18: J4.23, U3.29 (GPIO18)
/GPIO19: J4.21, U3.30 (GPIO19)
/GPIO20: J4.19, U3.31 (GPIO20)
/GPIO21: J4.17, U3.32 (GPIO21)
/GPIO22: J4.15, U3.34 (GPIO22)
/GPIO23: J4.13, U3.35 (GPIO23)
/GPIO24: J4.11, U3.36 (GPIO24)
/GPIO25: J4.9, U3.37 (GPIO25)
/GPIO26_ADC0: J4.7, U3.38 (GPIO26_ADC0)
/GPIO27_ADC1: J4.5, U3.39 (GPIO27_ADC1)
/GPIO28_ADC2: J4.3, U3.40 (GPIO28_ADC2)
/GPIO29_ADC3: J4.1, U3.41 (GPIO29_ADC3)
/INT1_ACCEL: U3.15 (GPIO12), U4.16 (INT1)
/INT2_ACCEL: U3.16 (GPIO13), U4.1 (INT2)
/INT3_GYRO: U3.17 (GPIO14), U4.12 (INT3)
/INT4_GYRO: U3.18 (GPIO15), U4.13 (INT4)
/INT_BARO: J4.27, U3.27 (GPIO16), U5.7 (INT)
/INT_MAG: J4.25, U3.28 (GPIO17), U6.A1 (INT)
/MISO: J3.7 (DAT0), U3.11 (GPIO8)
/MOSI: J3.3 (CMD), U3.14 (GPIO11)
/QSPI_SCLK: U2.6 (CLK), U3.52 (QSPI_SCLK)
/QSPI_SD0: U2.5 (DI(IO0)), U3.53 (QSPI_SD0)
/QSPI_SD1: U2.2 (DO(IO1)), U3.55 (QSPI_SD1)
/QSPI_SD2: U2.3 (IO2), U3.54 (QSPI_SD2)
/QSPI_SD3: U2.7 (IO3), U3.51 (QSPI_SD3)
/QSPI_SS: R1.1, R2.2, U2.1 (~CS), U3.56 (QSPI_SS)
/RUN: J4.29, U3.26 (RUN), U8.2
/SCL: U3.7 (GPIO5), U4.8 (SCL/SCK), U5.2 (SCK), U6.A3 (SCK)
/SCLK: J3.5 (CLK), U3.13 (GPIO10)
/SDA: U3.6 (GPIO4), U4.9 (SDA/SDI), U5.4 (SDI), U6.A2 (SDA)
/SWCLK: J4.33, U3.24 (SWCLK)
/SWD: J4.31, U3.25 (SWD)
/USB_D+: J1.3 (D+), R3.1
/USB_D-: J1.2 (D-), R4.1
/XIN: C2.1, U3.20 (XIN), Y1.1
/XOUT: R5.1, U3.21 (XOUT)
/~USB_BOOT: R1.2, U7.2
GND: C1.2, C2.2, C3.2, C4.2, C5.2, C6.2, C7.2, C8.2, C9.2, C10.2, C11.2, C12.2, C13.2, C14.2, C15.2, C16.2, C17.2, C18.2, C19.2, C20.2, C21.2, C22.2, C23.2, C24.1, J1.5 (GND), J1.6 (Shield), J3.6 (VSS), J3.G1 (GND), J3.G2 (GND__1), J3.G3 (GND__2), J3.G4 (GND__3), J4.2, J4.4, J4.6, J4.8, J4.10, J4.12, J4.14, J4.16, J4.18, J4.20, J4.22, J4.24, J4.26, J4.28, J4.30, J4.32, J4.34, J4.35, J4.36, U1.1 (GND), U2.4 (GND), U3.19 (TESTEN), U3.57 (GND), U4.2 (NC), U4.4 (GNDA), U4.6 (GNDIO), U4.10 (SDO2), U4.15 (SDO1), U5.3 (VSS), U5.5 (SDO), U5.8 (VSS), U5.9 (VSS), U6.B1 (GND), U6.B2 (ADSEL), U6.C3 (BYPASS), U7.1, U8.1, Y1.2, Y1.4
unnamed: C3.1, R5.2, Y1.3
unnamed: J3.2 (CD/DAT3), R6.2
unnamed: R4.2, U3.46 (USB_DM)
unnamed: R3.2, U3.47 (USB_DP)
VBUS: C1.1, J1.1 (VBUS), U1.3 (VI)

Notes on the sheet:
IOs
Power
Crystal
Make sure C8 is close to pin 45 of RP2040
SD Reader
Make sure C10 is close to pin 44 of RP2040
Make sure R3 and R4 are close to RP2040
Flash

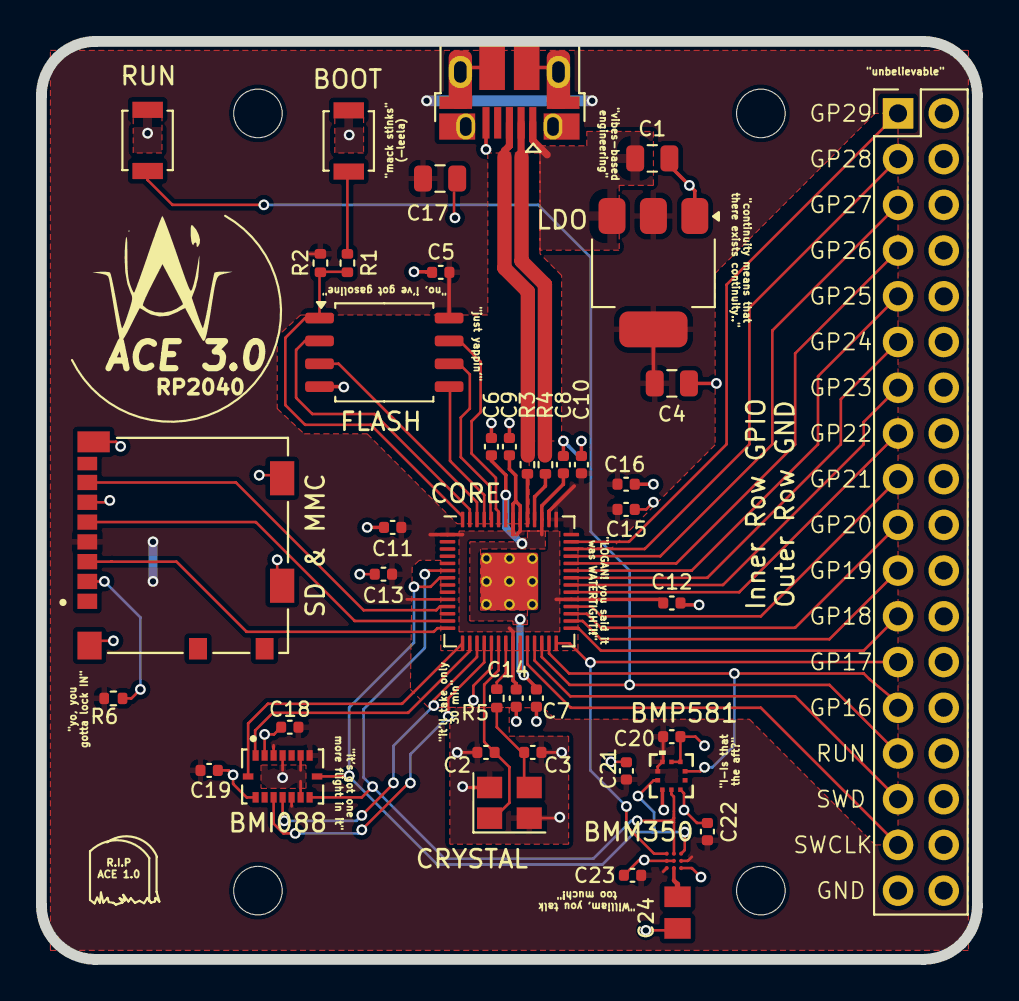
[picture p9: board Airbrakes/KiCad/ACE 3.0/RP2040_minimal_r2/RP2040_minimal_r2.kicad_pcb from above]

Board: 2 copper layers, 52.0 x 51.0 mm, 46 parts (0 on the bottom side), 46 nets.

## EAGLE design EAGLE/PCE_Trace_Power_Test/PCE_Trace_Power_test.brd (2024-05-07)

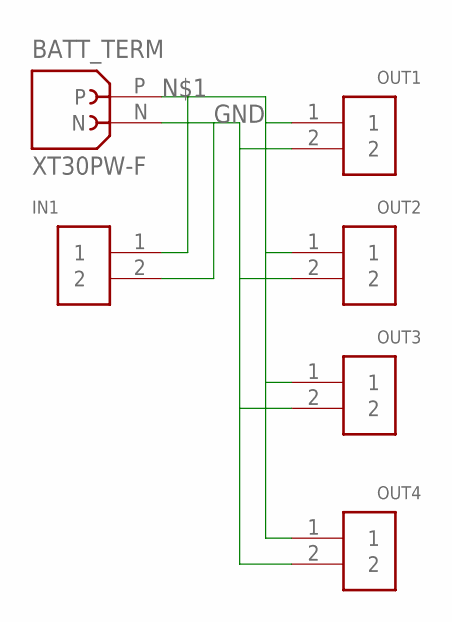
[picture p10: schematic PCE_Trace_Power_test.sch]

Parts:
BATT_TERM: XT30PW-F; AMASS_XT30PW-F
IN1: 282837-2; TE_282837-2
OUT1, OUT2, OUT3, OUT4: 282837-2; TE_282837-2

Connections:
GND: BATT_TERM.N, IN1.2, OUT1.2, OUT2.2, OUT3.2, OUT4.2
unnamed: BATT_TERM.P, IN1.1, OUT1.1, OUT2.1, OUT3.1, OUT4.1

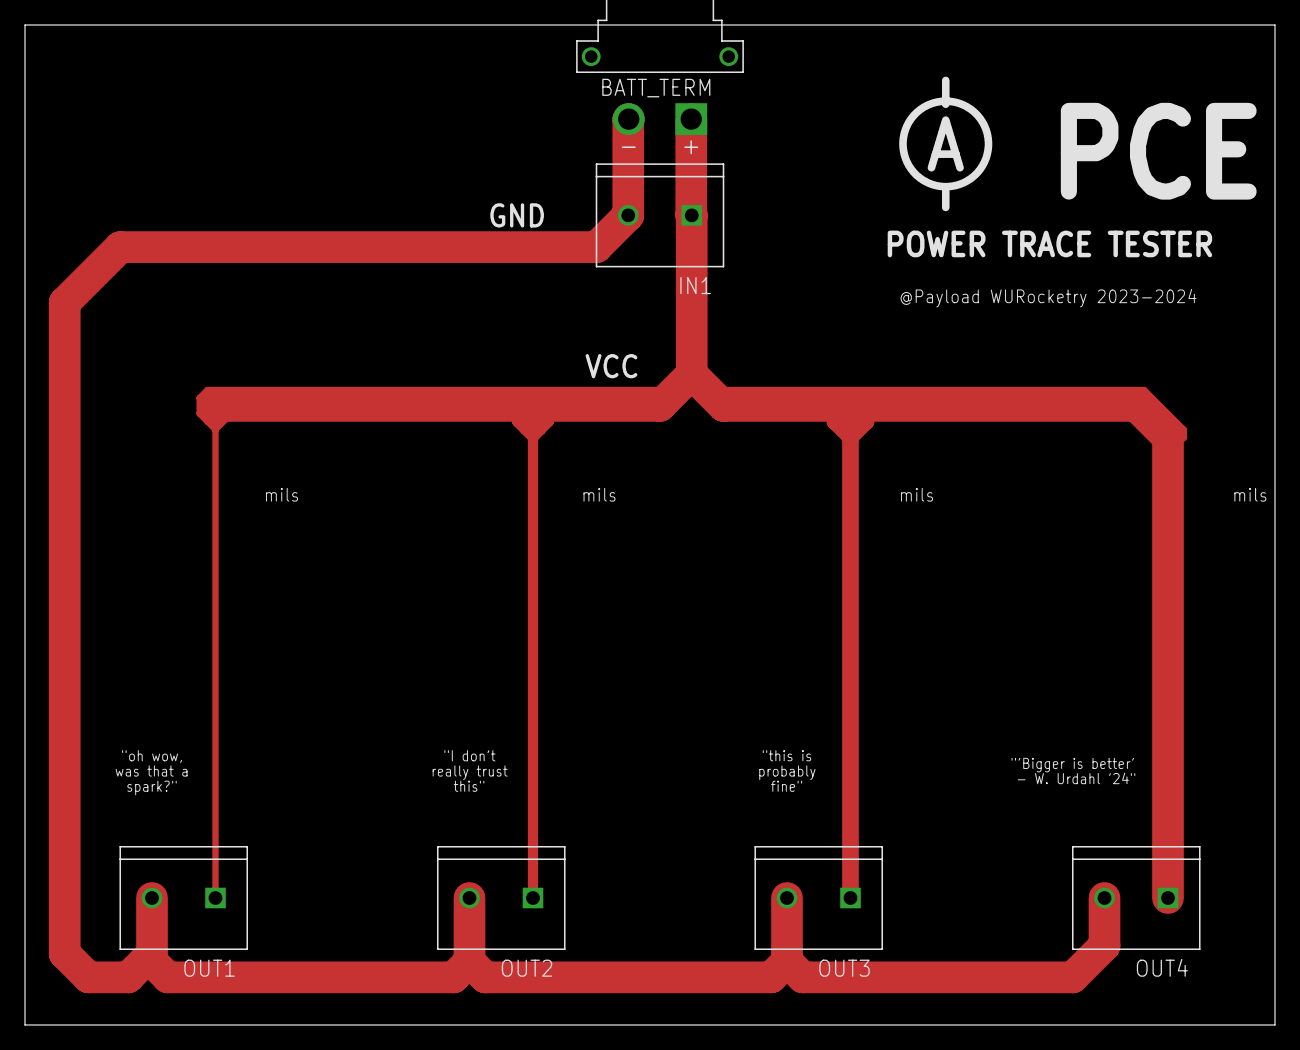
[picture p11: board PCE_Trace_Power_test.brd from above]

Board: 2 copper layers, 100.0 x 80.0 mm, 6 parts (0 on the bottom side), 2 nets.

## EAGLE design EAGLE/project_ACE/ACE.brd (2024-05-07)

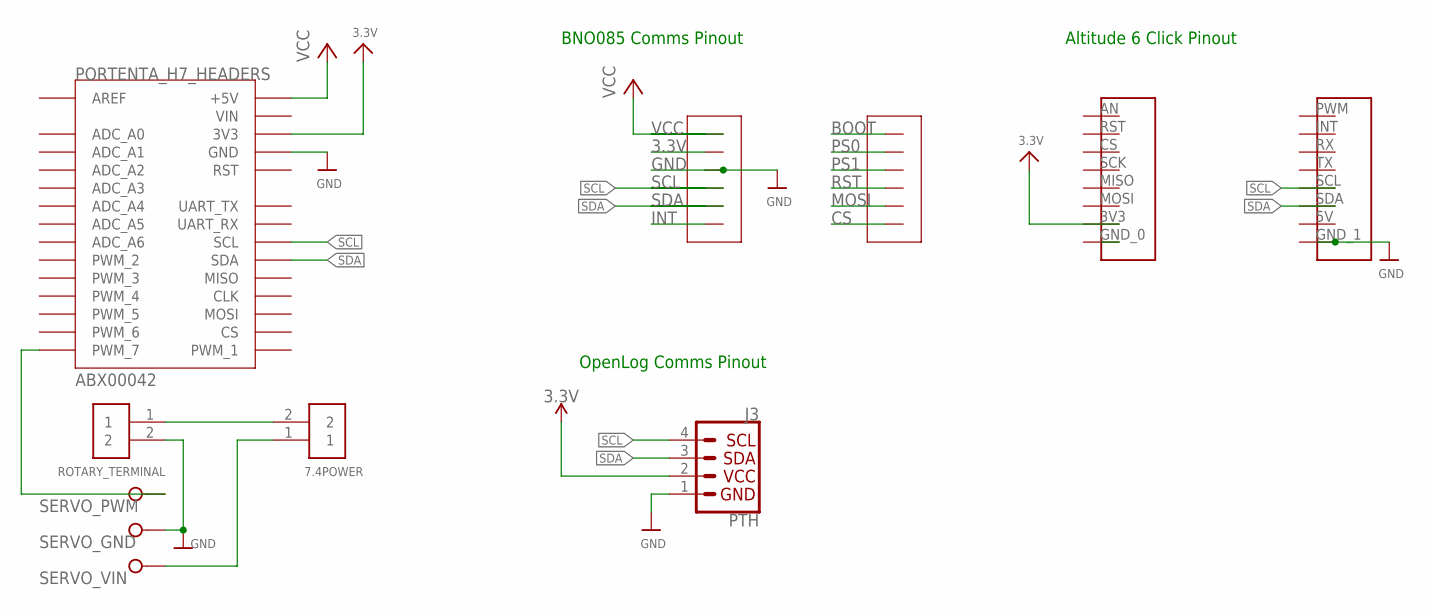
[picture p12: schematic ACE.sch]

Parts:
7.4POWER: 282837-2; TE_282837-2
J3: PTH; 1X04_NO_SILK
ROTARY_TERMINAL: 282837-2; TE_282837-2
SERVO: W237-3E
U$1: MIKROE-ALTITUDE-6-CLICK-DVC; MIKROE-ALTITUDE-6-CLICK-PINOUT
U$5: ADAFRUIT_BNO08X; ADAFRUIT_BNO08X_FOOTPRINT
U$10: ABX00042_HEADERS_IO; MODULE_ABX00042_HEADERS

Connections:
3.3V: J3.2 (VCC), U$1.3V3 (3.3V), U$10.J17 (3V3)
GND: J3.1 (GND), ROTARY_TERMINAL.2, SERVO.2, U$1.GND_1, U$5.GND, U$10.J18 (GND)
SCL: J3.4 (SCL), U$1.SCL, U$5.SCL, U$10.J22 (SCL)
SDA: J3.3 (SDA), U$1.SDA, U$5.SDA, U$10.J23 (SDA)
SERVO_GND: 7.4POWER.2, ROTARY_TERMINAL.1
SERVO_PWM: SERVO.1, U$10.J9 (PWM_7)
SERVO_VIN: 7.4POWER.1, SERVO.3
VCC: U$5.VIN (VCC), U$10.J15 (+5V)

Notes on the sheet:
OpenLog Comms Pinout
BNO085 Comms Pinout
Altitude 6 Click Pinout

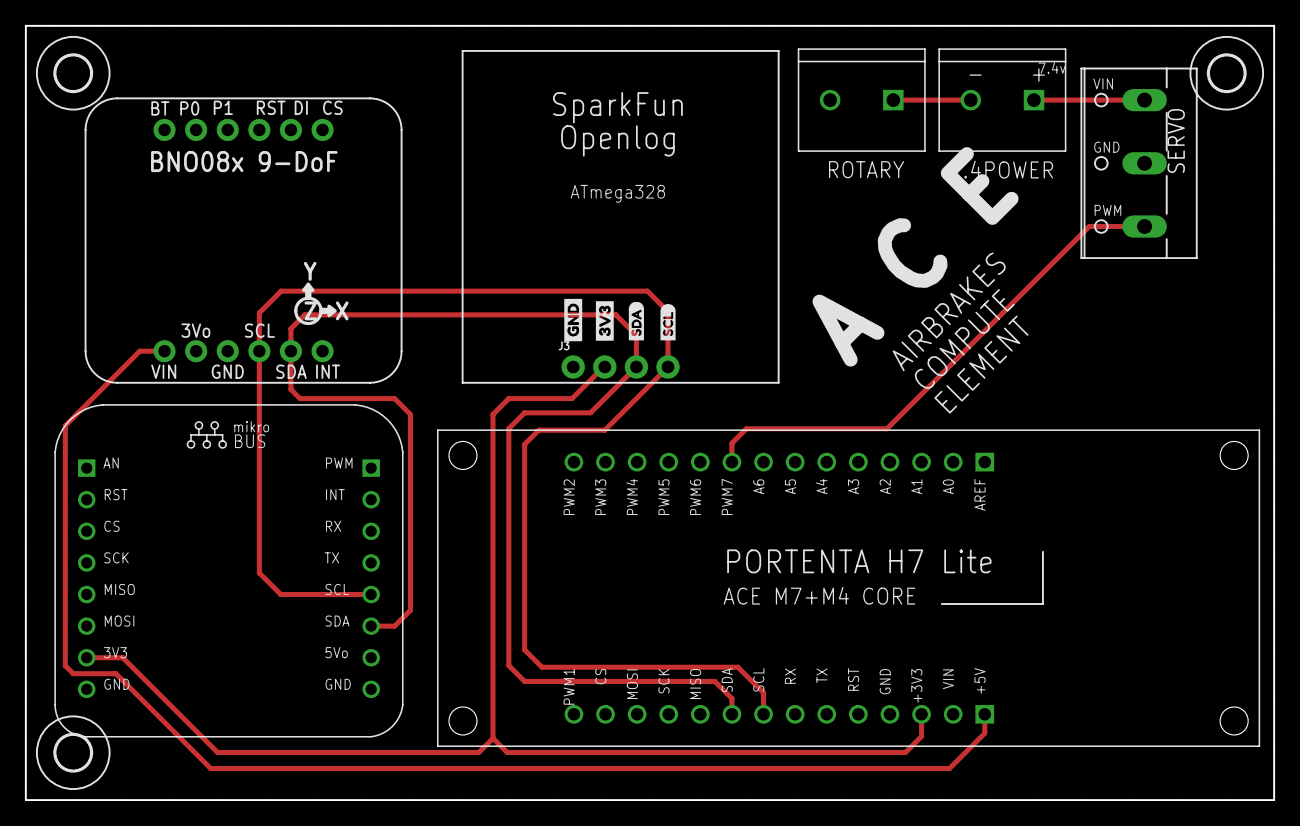
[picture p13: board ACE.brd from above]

Board: 2 copper layers, 100.3 x 62.2 mm, 14 parts (0 on the bottom side), 8 nets.

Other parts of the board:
U$8: 3V3-03
U$9: GND-03
U$13, U$14, U$15: 2,8
U$16: SDA1
U$19: SCL2

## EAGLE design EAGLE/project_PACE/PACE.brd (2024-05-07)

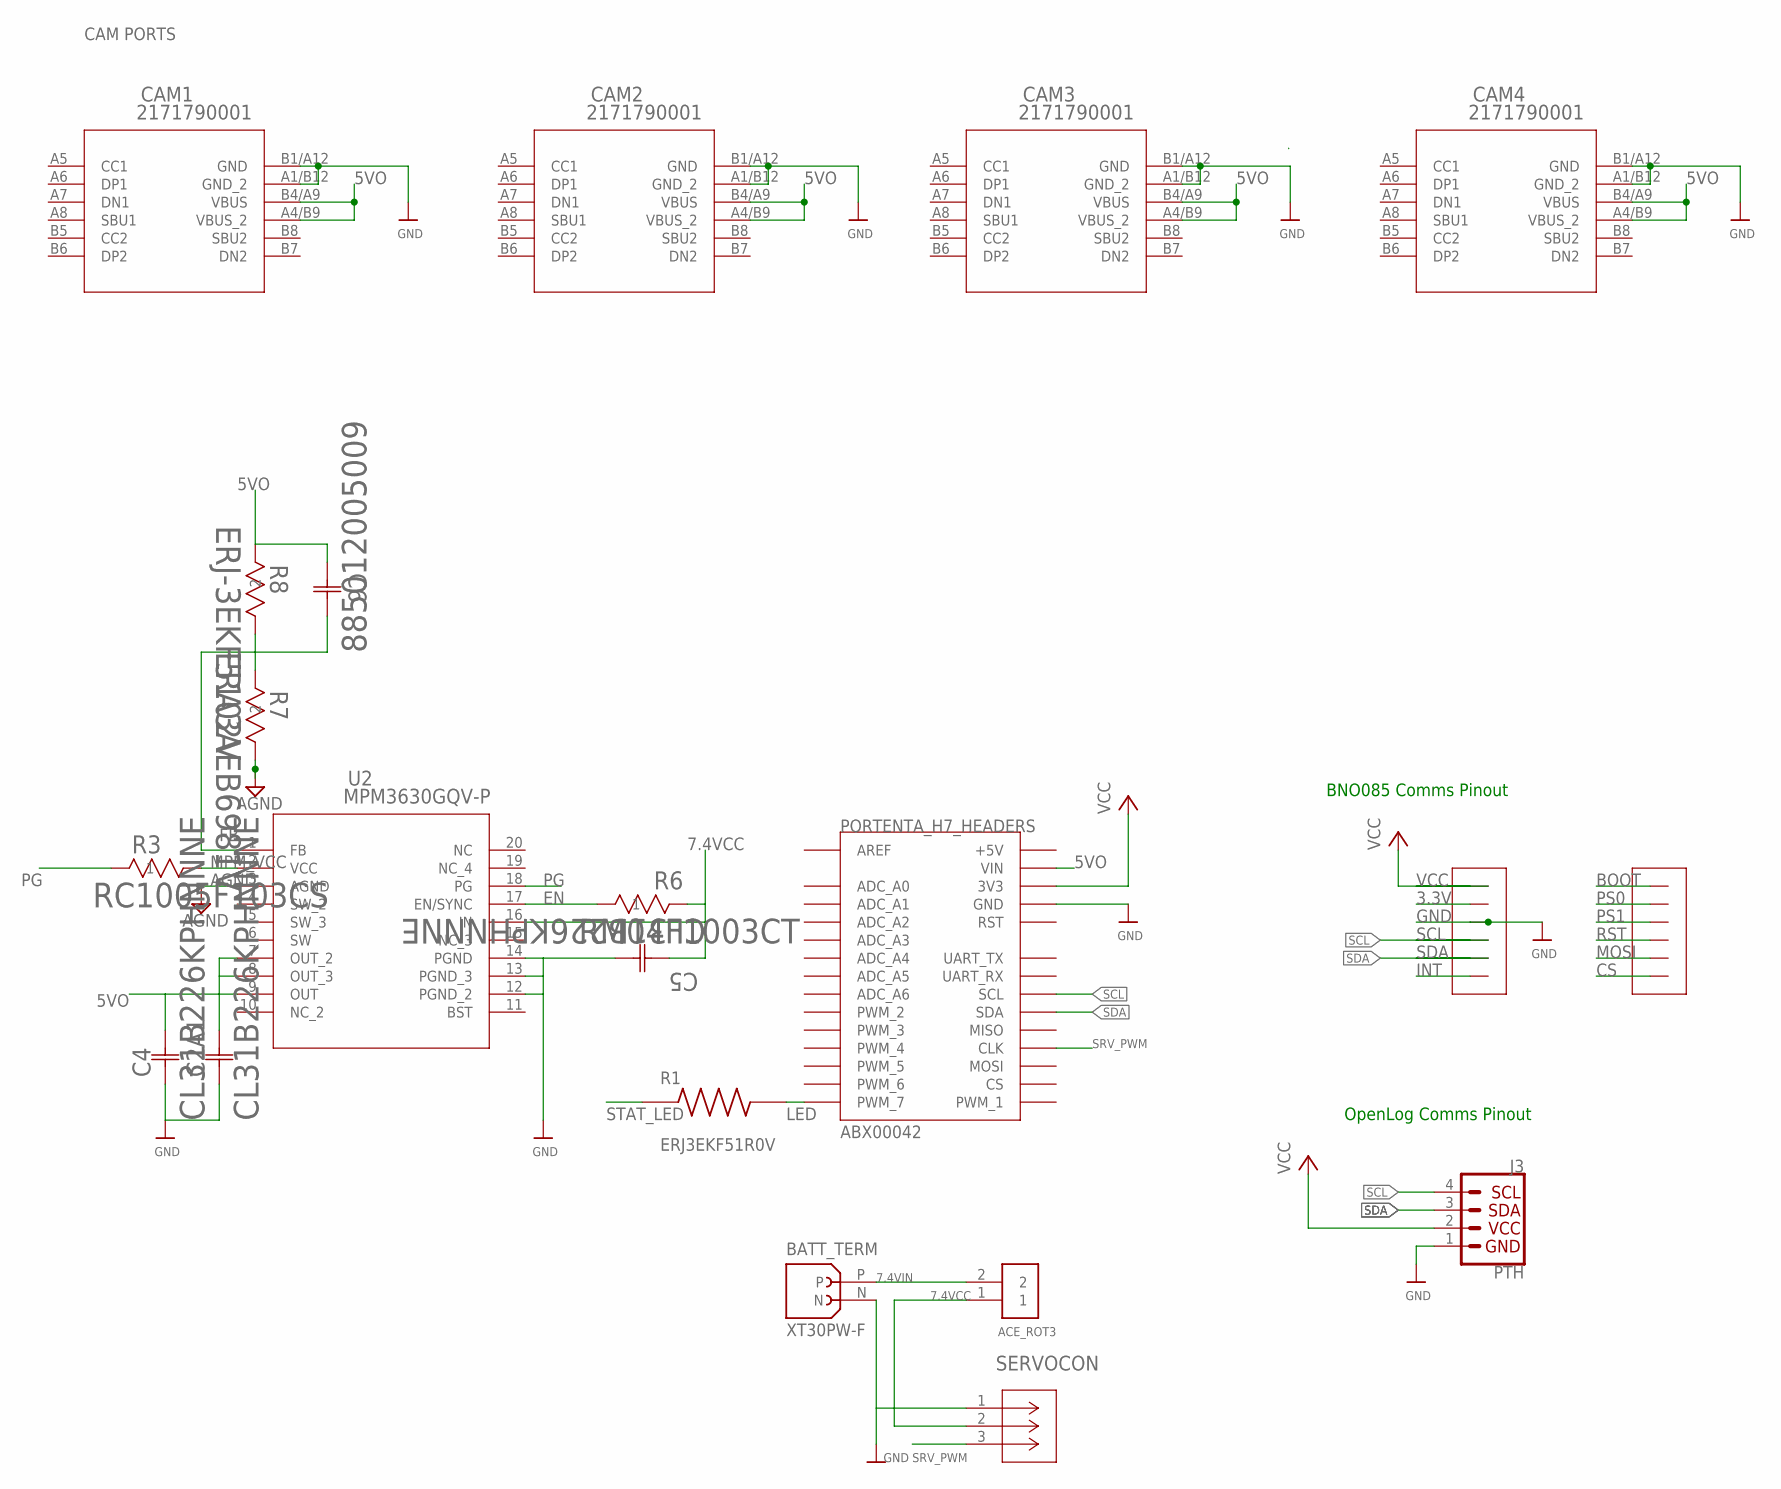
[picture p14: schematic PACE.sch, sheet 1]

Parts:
ACE_ROT3: 282837-2; TE_282837-2
BATT_TERM: XT30PW-F; AMASS_XT30PW-F
C2A1, C4, C5: CL31B226KPHNNNE; CAP_CL31_SAM
C6: 885012005009; CAP_885012005_WRE
CAM1, CAM2, CAM3, CAM4: 2171790001; 2171790001_MOL
J3: PTH; 1X04_NO_SILK
R1: ERJ3EKF51R0V; RES_ERJ3EKF51R0V
R3: RC1005F103CS; RES_1005_SAM
R6: RM04F1003CT; RES_RM04_CCE
R7: ERA3AEB6981V; RES_ERA3A_0603_PAN
R8: ERJ-3EKF5102V; RC0603N_PAN
SERVOCON: B03B-PASK-1_(LF)_(SN); CONN_B03B-PASK-1_(LF)_(SN)_JST
U2: MPM3630GQV-P; QFN3P0X5P0X1P6_MPM3630_MNP
U$5: ADAFRUIT_BNO08X; ADAFRUIT_BNO08X_FOOTPRINT
U$10: ABX00042_HEADERS_IO; MODULE_ABX00042_HEADERS

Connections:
5VO: C2A1.2, C4.2, C6.2, CAM1.A4/B9 (VBUS_2), CAM1.B4/A9 (VBUS), CAM2.A4/B9 (VBUS_2), CAM2.B4/A9 (VBUS), CAM3.A4/B9 (VBUS_2), CAM3.B4/A9 (VBUS), CAM4.A4/B9 (VBUS_2), CAM4.B4/A9 (VBUS), R8.2, U2.7 (OUT_2), U2.8 (OUT_3), U2.9 (OUT), U$10.J16 (VIN)
7.4VCC: ACE_ROT3.1, C5.1, R6.2, SERVOCON.2, U2.16 (IN)
7.4VIN: ACE_ROT3.2, BATT_TERM.P
AGND: R7.1, U2.3 (AGND)
EN: R6.1, U2.17 (EN/SYNC)
FB: C6.1, R7.2, R8.1, U2.1 (FB)
GND: BATT_TERM.N, C2A1.1, C4.1, C5.2, CAM1.A1/B12 (GND_2), CAM1.B1/A12 (GND), CAM2.A1/B12 (GND_2), CAM2.B1/A12 (GND), CAM3.A1/B12 (GND_2), CAM3.B1/A12 (GND), CAM4.A1/B12 (GND_2), CAM4.B1/A12 (GND), J3.1 (GND), SERVOCON.1, U2.12 (PGND_2), U2.13 (PGND_3), U2.14 (PGND), U$5.GND, U$10.J18 (GND); also elsewhere on the board
LED: R1.2, U$10.J9 (PWM_7)
MPM_VCC: R3.2, U2.2 (VCC)
PG: R3.1, U2.18 (PG)
SCL: J3.4 (SCL), U$5.SCL, U$10.J22 (SCL); also elsewhere on the board
SDA: J3.3 (SDA), U$5.SDA, U$10.J23 (SDA); also elsewhere on the board
SRV_PWM: SERVOCON.3, U$10.J25 (CLK)
STAT_LED: R1.1
VCC: J3.2 (VCC), U$5.VIN (VCC), U$10.J17 (3V3); also elsewhere on the board

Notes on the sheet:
OpenLog Comms Pinout
BNO085 Comms Pinout
CAM PORTS

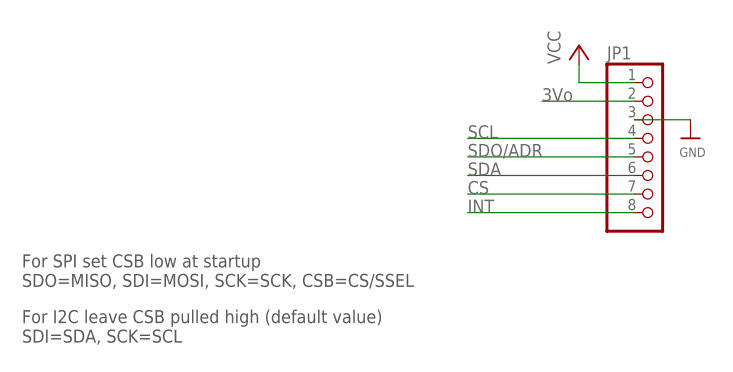
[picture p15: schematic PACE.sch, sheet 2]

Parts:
JP1: HEADER-1X870MIL; 1X08_ROUND_70

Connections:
CS: JP1.7
GND: JP1.3; also elsewhere on the board
INT: JP1.8
SCL: JP1.4; also elsewhere on the board
SDA: JP1.6; also elsewhere on the board
SDO/ADR: JP1.5
VCC: JP1.1; also elsewhere on the board

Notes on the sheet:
For SPI set CSB low at startup SDO=MISO, SDI=MOSI, SCK=SCK, CSB=CS/SSEL
For I2C leave CSB pulled high (default value) SDI=SDA, SCK=SCL
3Vo


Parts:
JP2: HEADER-1X670MIL; 1X06_ROUND_70
JP3: HEADER-1X4ROUND; 1X04_ROUND

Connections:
CS-1: JP3.4
GND: JP2.3, JP3.1; also elsewhere on the board
INT1: JP2.6
INT2: JP3.2
SCL: JP2.4; also elsewhere on the board
SDA: JP2.5; also elsewhere on the board
SDO: JP3.3
VCC: JP2.1; also elsewhere on the board


Board: 2 copper layers, 114.0 x 63.0 mm, 33 parts (0 on the bottom side), 14 nets.

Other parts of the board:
JP4, JP5: STAND-OFF
U$8: 3V3-03
U$9: GND-03
U$13, U$14, U$15, U$29: 2,8
U$16: SDA1
U$19: SCL2

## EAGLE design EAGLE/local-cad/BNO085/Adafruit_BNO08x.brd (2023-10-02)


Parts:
C1, C4, C5: 0.1uF; 0603-NO
C2, C3: 10uF; 0805-NO
C6, C7: 22pF; 0603-NO
CONN3, CONN4: STEMMA_I2C_QT; JST_SH4
D1: GREEN; CHIPLED_0603_NOOUTLINE
FID3, FID4: FIDUCIAL_1MM
JP1, JP2: HEADER-1X670MIL; 1X06_ROUND_70
Q2: BSS138; SOT363
R2, R3, R4: 10K; RESPACK_4X0603
SJ1: PS1; SOLDERJUMPER_ARROW_NOPASTE
SJ2: PS0; SOLDERJUMPER_ARROW_NOPASTE
U1: BNO080
U2: AP2112K-3.3; SOT23-5
U3: 74AHC4050; TSSOP16
U$1, U$17, U$19, U$21: MOUNTINGHOLE2.5; MOUNTINGHOLE_2.5_PLATED
X1: 32.768; XTAL3215

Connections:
3.3V: C1.1, C3.1, C5.1, JP1.2, Q2.2 (G), Q2.5 (G), R2.5 (2), R3.3 (1), R3.5 (2), U1.3 (VDD), U1.28 (VDDIO), U2.5 (OUT), U3.1 (VCC)
BOOT: JP2.1, R2.3 (1), U3.7 (3A)
BOOT_3V: U1.4 (BOOTN), U3.6 (3Y)
CAP: C4.2, U1.9 (CAP)
CS: JP2.6, R4.1, U3.9 (4A)
CS_3V: U1.18 (H_CSN), U3.10 (4Y)
GND: C1.2, C2.2, C3.2, C4.1, C5.2, C6.2, C7.2, CONN3.1 (GND), CONN3.MT1 (MT), CONN3.MT2 (MT), CONN4.1 (GND), CONN4.MT1 (MT), CONN4.MT2 (MT), D1.C, JP1.3, R2.7 (2), R2.8 (2), R3.1, R3.2 (1), R3.8 (2), U1.2 (GND), U1.10 (CLKSEL0), U1.25 (GNDIO), U2.2 (GND), U3.8 (GND)
INT: JP1.6, U1.14 (H_INTN)
MOSI: JP2.5, R3.7 (2), U3.11 (5A)
MOSI_3V: U1.17 (H_SA0/MOSI), U3.12 (5Y)
unnamed: D1.A, R2.4 (1)
PS0: JP2.2, R2.2 (1), SJ2.2, U3.3 (1A)
PS0_3V: U1.6 (PS0/WAKE), U3.2 (1Y)
PS1: JP2.3, R2.1, SJ1.2, U3.5 (2A)
PS1_3V: U1.5 (PS1), U3.4 (2Y)
RST: JP2.4, R4.2 (1), U3.14 (6A)
RST_3V: U1.11 (NRST), U3.15 (6Y)
SCL/SCK/RX: CONN3.4 (SCL), CONN4.4 (SCL), JP1.4, Q2.6 (D), R4.4 (1)
SCL_3V: Q2.1 (S), R3.4 (1), U1.19 (H_SCL/SCLK/RX)
SDA/MISO/TX: CONN3.3 (SDA), CONN4.3 (SDA), JP1.5, Q2.3 (D), R4.3 (1)
SDA_3V: Q2.4 (S), R3.6 (2), U1.20 (H_SDA/MISO/TX)
VCC: C2.1, CONN3.2 (V+), CONN4.2 (V+), JP1.1, R2.6 (2), R4.5 (2), R4.6 (2), R4.7 (2), R4.8 (2), SJ1.1, SJ2.1, U2.1 (IN), U2.3 (EN)
XIN: C6.1, U1.27 (XIN32), X1.P$1
XOUT: C7.1, U1.26 (CLKSEL1/XOUT32), X1.P$2

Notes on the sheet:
I2C Pullups & Shift
STEMMA/I2C Headers
ON LED
Power supply
Default Bus = I2C
Close PS1 for UART Close PS1 and PS0 for SPI
SA0 is default low, so I2C ADDR = 1001010 (0x4A)



Board: 2 copper layers, 25.4 x 22.9 mm, 32 parts (5 on the bottom side), 24 nets.

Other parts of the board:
U$22: ADAFRUIT_3.5MM
U$25: PCBFEAT-REV-040
U$30, U$31: STEMMAQT

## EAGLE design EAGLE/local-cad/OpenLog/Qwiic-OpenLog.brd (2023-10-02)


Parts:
ADR: SOLDERJUMPERNO; SJ_2S-NO
C1: 4.7uF; 0603
C2, C3: 0.1uF; 0603
D1: RED; LED-0603
D3: GREEN; LED-0603
FID1, FID2, FID3, FID4: FIDUCIALUFIDUCIAL; FIDUCIAL-MICRO
FRAME1: FRAME-LETTER; CREATIVE_COMMONS
I2C: JUMPER-SMT_3_2-NC_TRACE_SILK; SMT-JUMPER_3_2-NC_TRACE_SILK
J1: MICRO-SD; MICRO-SD-SOCKET
J2, J4: SMD; 1X04_1MM_RA
J3: PTH; 1X04_NO_SILK
J5: ISP; 2X3_TEST_POINTS
J6: CONN_06NO_SILK_NO_POP; 1X06_NO_SILK
JP3, JP4: STAND-OFF
LOGO1: SFE_LOGO_FLAME.1_INCH; SFE_LOGO_FLAME_.1
LOGO2: OSHW-LOGOMINI; OSHW-LOGO-MINI
LOGO4: SFE_LOGO_NAME_FLAME.1_INCH; SFE_LOGO_NAME_FLAME_.1
Q1: 16MHZ; RESONATOR-SMD
R1: 1k; 0603
R2, R3: 10k; 0603
R4, R5: 2.2k; 0603
R6: 330; 0603
U2: ATMEGA328P; TQFP32-08

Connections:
3.3V: C1.1, C3.2, I2C.2, J1.VCC, J2.2, J3.2 (VCC), J4.2, J5.2, J6.3, R2.2, R3.2, U2.4 (VCC), U2.6 (VCC), U2.18 (AVCC), U2.20 (AREF)
ADDR: ADR.2, U2.1 (PD3(INT1))
CS: J1.CS, R3.1, U2.14 (PB2(SS/OC1B))
DTR: C2.2, J6.6
GND: ADR.1, C1.2, C3.1, D1.C, D3.C, J1.GND, J2.1, J3.1 (GND), J4.1, J5.6, J6.1, J6.2, Q1.2, U2.3 (GND), U2.5 (GND), U2.21 (AGND)
MISO: J1.DO, J5.1, U2.16 (PB4(MISO))
MOSI: J1.DI, J5.4, U2.15 (PB3(MOSI/OC2))
unnamed: Q1.1, U2.8 (PB7(XTAL2/TOSC2))
unnamed: Q1.3, U2.7 (PB6(XTAL1/TOSC1))
unnamed: D1.A, R1.2
unnamed: R1.1, U2.9 (PD5(T1))
unnamed: I2C.1, R5.2
unnamed: I2C.3, R4.2
unnamed: D3.A, R6.2
RST: C2.1, J5.5, R2.1, U2.29 (PC6(/RESET))
RXI: J6.4, U2.30 (PD0(RXD))
SCK: J1.SCLK (SCK), J5.3, R6.1, U2.17 (PB5(SCK))
SCL: J2.4, J3.4 (SCL), J4.4, R4.1, U2.28 (PC5(ADC5/SCL))
SDA: J2.3, J3.3 (SDA), J4.3, R5.1, U2.27 (PC4(ADC4/SDA))
TXO: J6.5, U2.31 (PD1(TXD))

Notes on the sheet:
This board is meant to be used with Qwiic. The boot header is meant for Serial Basic connection for programming.
V12
N. Seidle
I2C Pull-up
Communication
MicroSD Socket
ISP Header
7-Bit I2C Address Jumper
Closed = 0x29
Open (default) = 0x2A



Board: 2 copper layers, 25.4 x 26.7 mm, 49 parts (17 on the bottom side), 20 nets.

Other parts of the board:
U$3: QWIIC-LOGO-SMALL
U$4: 3V3-03
U$5: GND-03
U$6: 3V30
U$7: ADR-()-03
U$8: I_SUPER2_C-()-03
U$9: PWR-()-03
U$10: BLK3
U$11: BOOT5
U$12: GRN4
U$13, U$16: SDA1
U$14: QWIIC7
U$15, U$19: SCL2
U$17: STAT0
U$18: OPENLOG0
U$20: GND1

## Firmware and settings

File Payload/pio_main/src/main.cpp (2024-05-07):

#include <Arduino.h>
#include <algorithm>
#include <bitset>
#include <Adafruit_Sensor.h>
#include <Adafruit_BNO08x.h>
#include "Adafruit_BME680.h"
#include <Adafruit_GPS.h>
#include "SparkFun_Qwiic_OpenLog_Arduino_Library.h"
#include "Adafruit_MAX1704X.h"
#include <RadioLib.h>
#include <Adafruit_NeoPixel.h>
// #include <SoftwareSerial.h>

// Forward declare
void ErrorLEDLoop(const char*);
void logData(const char* componentName, float secondsSinceOn, float* data, int dataSize);
int getNumberOfPrevFlights();

// Define sensor objects
Adafruit_BNO08x bno08x;
Adafruit_BME680 bme;
Adafruit_GPS GPS(&Wire);
OpenLog logger;
Adafruit_MAX17048 maxlipo;

// Struct for Euler angles
struct euler_t {
  float yaw;
  float pitch;
  float roll;
} ypr;

//enum for global array indices
enum{
  BNO_YAW,
  BNO_PITCH,
  BNO_ROLL,
  BNO_XACCEL,
  BNO_YACCEL,
  BNO_ZACCEL,
  SECONDS_SINCE_ON,
  BME_TEMPERATURE,
  BME_PRESSURE,
  BME_HUMIDITY,
  BME_GAS,
  BME_ALTITUDE,
  GPS_HOUR,
  GPS_MINUTE,
  GPS_SPEED,
  GPS_LATITUDE,
  GPS_LONGITUDE,
  GPS_ALTITUDE,
  BATTERY_PERCENT,
  BATTERY_VOLTAGE,
  BATTERY_DISCHARGE_RATE,
  ENUM_SIZE, 
};

const char* ENUM_NAMES[] = {
  "BNO_YAW",
  "BNO_PITCH",
  "BNO_ROLL",
  "BNO_XACCEL",
  "BNO_YACCEL",
  "BNO_ZACCEL",
  "SECONDS_SINCE_ON",
  "BME_TEMPERATURE",
  "BME_PRESSURE",
  "BME_HUMIDITY",
  "BME_GAS",
  "BME_ALTITUDE",
  "GPS_HOUR",
  "GPS_MINUTE",
  "GPS_SPEED",
  "GPS_LATITUDE",
  "GPS_LONGITUDE",
  "GPS_ALTITUDE",
  "BATTERY_PERCENT",
  "BATTERY_VOLTAGE",
  "BATTERY_DISCHARGE_RATE_%_PER_HOUR",
};

//Global Sensor Data Array
double DATA_COMPONENT_READINGS[ENUM_SIZE];

//Neopixel Definitions
const int pin = 4;
const int numPixels = 1;
Adafruit_NeoPixel pixels = Adafruit_NeoPixel(numPixels, pin, NEO_GRB + NEO_KHZ800);

//BNO Defintions
sh2_SensorValue_t sensorValue;
sh2_SensorId_t reportType = SH2_ARVR_STABILIZED_RV;
long reportIntervalUs = 5000;

// BME680 Definitions 
#define SEALEVELPRESSURE_HPA (1013.25)

//GPS Defintions
uint32_t timer = millis();

//Openlog Defintions
const byte OpenLogAddress = 42;
String filename;
String smallFileName;

//Battery Monitor Defintions
float lastBatteryVoltage = 0.0;
unsigned long lastBatteryCheck = 0;  

//LoRa Defintions
#define FREQ 916.23
#define TRANSMIT_PWR 20
#define RFM95_CS    16  // Chip select pin
#define RFM95_RST   17  // Reset pin
#define RFM95_IRQ   21  // Interrupt pin, connected to DIO0
#define RFM95_GPIO  22  // Additional GPIO, connected to DIO1
RFM95 radio = new Module(RFM95_CS, RFM95_IRQ, RFM95_RST, RFM95_GPIO);
int16_t packetnum = 0;  

//Define timing separations for devices
float bnoTime = 342;
float bmeTime = 234;
float gpsTime = 1234;
float batteryTime = 2354;
float rfTime = 756;

unsigned long bnoTimer = 0;
unsigned long bmeTimer = 0;
unsigned long gpsTimer = 0;
unsigned long batteryTimer = 0;
unsigned long rfTimer = 0;


void setup() {
  Serial.begin(115200);
  pinMode(LED_BUILTIN, OUTPUT);

  //LoRa Setup
  pinMode(RFM95_RST, OUTPUT);
  digitalWrite(RFM95_RST, HIGH);

  //LoRa Manual Reset
  digitalWrite(RFM95_RST, LOW);
  delay(10);
  digitalWrite(RFM95_RST, HIGH);
  delay(10);
  
  //Turn Radio On
  int state = radio.begin();
  if (state == RADIOLIB_ERR_NONE) {
    // no error
    Serial.println(F("Initialization successful!"));
  } else {
    while(true){
      Serial.print(F("Error: "));
      Serial.println(state);
      delay(1000);
    }
  }

  //Set Radio Transmit Power
  state = radio.setOutputPower(TRANSMIT_PWR, false);
  if(state == RADIOLIB_ERR_NONE) {
    Serial.print(F("Transmit Power set to: "));
    Serial.print(TRANSMIT_PWR);
    Serial.println(F(" dBm"));
  } else {
    Serial.print(F("Setting Output Power Failed:, code "));
    Serial.println(state);
  }

  //Set Radio Frequency 
  state = radio.setFrequency(FREQ);
  if(state == RADIOLIB_ERR_NONE) {
    Serial.print(F("Frequency set to: "));
    Serial.print(FREQ);
    Serial.println(F(" MHz"));
  } else {
    Serial.print(F("Setting frequency failed, code "));
    Serial.println(state);
  }

  //Initialize BNO
  if (!bno08x.begin_I2C()) {
    ErrorLEDLoop("Failed to find BNO08x IMU, Halting");
  }
  if (!bno08x.enableReport(reportType, reportIntervalUs)) {
    Serial.println("Could not enable stabilized remote vector for IMU");
  }


  //Initialize BME
  if (!bme.begin()) {
    ErrorLEDLoop("Failed to find BME680 sensor, Halting");
  }
  bme.setTemperatureOversampling(BME680_OS_8X);
  bme.setHumidityOversampling(BME680_OS_2X);
  bme.setPressureOversampling(BME680_OS_4X);
  bme.setIIRFilterSize(BME680_FILTER_SIZE_3);
  bme.setGasHeater(320, 150);

  //Initialize GPS
  GPS.begin(0x10);  // The I2C address to use is 0x10
  GPS.sendCommand(PMTK_SET_NMEA_OUTPUT_RMCGGA);
  GPS.sendCommand(PMTK_SET_NMEA_UPDATE_1HZ); // 1 Hz update rate
  GPS.sendCommand(PGCMD_ANTENNA);
  delay(1000);
  GPS.println(PMTK_Q_RELEASE);

  //Initialize Openlog
  Wire.begin();
  logger.begin();
  int fileCount = getNumberOfPrevFlights();
  filename = "flight_" + String(fileCount) + ".txt";
  Serial.println("Writing this flights data to: " + filename);

  bmeTimer = millis();
  bnoTimer = millis();
  gpsTimer = millis();
  batteryTimer = millis();
  rfTimer = millis();
}

double secondsSinceOn(){
  return millis()/1000.0;
}

void ErrorLEDLoop(const char* error_msg){
  pixels.begin();
  pixels.setBrightness(255);
  while(true){
    Serial.println(error_msg);
    pixels.setPixelColor(0, pixels.Color(255, 0, 0));
    pixels.show();
    delay(1000);                      
    pixels.setPixelColor(0, pixels.Color(0, 0, 0));
    pixels.show();
    delay(1000);    
  }                
}

void quaternionToEulerRV(sh2_RotationVectorWAcc_t* rotational_vector, euler_t* ypr, bool degrees = false) {
  float sqr = sq(rotational_vector->real);
  float sqi = sq(rotational_vector->i);
  float sqj = sq(rotational_vector->j);
  float sqk = sq(rotational_vector->k);

  ypr->yaw = atan2(2.0 * (rotational_vector->i * rotational_vector->j + rotational_vector->k * rotational_vector->real), (sqi - sqj - sqk + sqr));
  ypr->pitch = asin(-2.0 * (rotational_vector->i * rotational_vector->k - rotational_vector->j * rotational_vector->real) / (sqi + sqj + sqk + sqr));
  ypr->roll = atan2(2.0 * (rotational_vector->j * rotational_vector->k + rotational_vector->i * rotational_vector->real), (-sqi - sqj + sqk + sqr));

  if (degrees) {
    ypr->yaw *= RAD_TO_DEG;
    ypr->pitch *= RAD_TO_DEG;
    ypr->roll *= RAD_TO_DEG;
  }
}

// Function to collect data from BNO08x
void collectDataFromBNO() {
  unsigned long currentMillis = millis();
  if (currentMillis >= bnoTime + bnoTimer) {
    bnoTimer += bnoTime;
    if (bno08x.wasReset()) {
      Serial.print("sensor was reset ");
      bno08x.enableReport(reportType, reportIntervalUs);
    }
   
    if (bno08x.getSensorEvent(&sensorValue)) {
      if (sensorValue.sensorId == reportType) {
        quaternionToEulerRV(&sensorValue.un.arvrStabilizedRV, &ypr, true);
 
        DATA_COMPONENT_READINGS[BNO_YAW] = ypr.yaw;
        DATA_COMPONENT_READINGS[BNO_PITCH] = ypr.pitch;
        DATA_COMPONENT_READINGS[BNO_ROLL] = ypr.roll;

        DATA_COMPONENT_READINGS[BNO_XACCEL] = sensorValue.un.accelerometer.x;
        DATA_COMPONENT_READINGS[BNO_YACCEL] = sensorValue.un.accelerometer.y;
        DATA_COMPONENT_READINGS[BNO_ZACCEL] = sensorValue.un.accelerometer.z;

        DATA_COMPONENT_READINGS[SECONDS_SINCE_ON] = secondsSinceOn();

        const char* componentName = "BNO";
        float data[6];
        data[0] = DATA_COMPONENT_READINGS[BNO_YAW];
        data[1] = DATA_COMPONENT_READINGS[BNO_PITCH];
        data[2] = DATA_COMPONENT_READINGS[BNO_ROLL];
        data[3] = DATA_COMPONENT_READINGS[BNO_XACCEL];
        data[4] = DATA_COMPONENT_READINGS[BNO_YACCEL];
        data[5] = DATA_COMPONENT_READINGS[BNO_ZACCEL];

        logData(componentName, secondsSinceOn(), data, 6); 

      }
    } 
  }
}

// Function to collect data from BME680
/*
The bme.performReading() function is blocking, it takes like 3 seconds to run. The delta timing loop is useless
since the program will get stuck on the if-statement for 3 seconds before taking any other measurements. To avoid
this we updated the delta timing loop to update every 3200 milliseconds (needs more testing) and we asynchronously collect the data by using 'beginReading()' and then 'endReading()' Still needs more testing to find out what the largest time it may take to gather that data. Probably around 3000. --Chase

*/
void collectDataFromBME() {
  unsigned long currentMillis = millis();
  if (currentMillis >= bmeTimer) {
    bmeTimer += bmeTime;
    if (bme.beginReading()) {

      DATA_COMPONENT_READINGS[BME_TEMPERATURE] = bme.temperature;
      DATA_COMPONENT_READINGS[BME_PRESSURE] = bme.pressure;
      DATA_COMPONENT_READINGS[BME_HUMIDITY] = bme.humidity;
      DATA_COMPONENT_READINGS[BME_GAS] = bme.gas_resistance / 1000.0;
      DATA_COMPONENT_READINGS[BME_ALTITUDE] = bme.readAltitude(SEALEVELPRESSURE_HPA);

      const char* componentName = "BME";
      float data[5];
      data[0] = DATA_COMPONENT_READINGS[BME_TEMPERATURE];
      data[1] = DATA_COMPONENT_READINGS[BME_PRESSURE];
      data[2] = DATA_COMPONENT_READINGS[BME_HUMIDITY];
      data[3] = DATA_COMPONENT_READINGS[BME_GAS];
      data[4] = DATA_COMPONENT_READINGS[BME_ALTITUDE];
      logData(componentName, DATA_COMPONENT_READINGS[SECONDS_SINCE_ON], data, 5); 

    }
     else {
      Serial.println("Failed to perform BME680 reading");
    }
    bme.endReading();
  }
}

void collectDataFromGPS() {
  // Read data from the GPS
  char c = GPS.read();

  // Check if a sentence is received
  if (GPS.newNMEAreceived()) {
    if (!GPS.parse(GPS.lastNMEA()))
      return; // Fail to parse a sentence
  }

  // Update GPS data every 2 seconds
  unsigned long currentMillis = millis();
  if (currentMillis - gpsTimer >= 2000) { // Corrected timing logic
    gpsTimer = currentMillis; // Reset timer for the next interval

    if (GPS.fix) {
      // Convert N/S, E/W degrees to decimal format for Google Maps
      float lat = GPS.latitude / 100;
      int latDegrees = (int)lat;
      float latMinutes = (lat - latDegrees) * 100;
      float decimalLat = latDegrees + (latMinutes / 60);
      if (GPS.lat == 'S') decimalLat *= -1;

      float lon = GPS.longitude / 100;
      int lonDegrees = (int)lon;
      float lonMinutes = (lon - lonDegrees) * 100;
      float decimalLon = lonDegrees + (lonMinutes / 60);
      if (GPS.lon == 'W') decimalLon *= -1;

      // Store the converted values
      DATA_COMPONENT_READINGS[GPS_LATITUDE] = decimalLat;
      DATA_COMPONENT_READINGS[GPS_LONGITUDE] = decimalLon;
      DATA_COMPONENT_READINGS[GPS_HOUR] = GPS.hour;
      DATA_COMPONENT_READINGS[GPS_SPEED] = GPS.speed;
      DATA_COMPONENT_READINGS[GPS_ALTITUDE] = GPS.altitude;

      const char* componentName = "GPS";
      float data[5] = {decimalLat, decimalLon, GPS.hour, GPS.speed, GPS.altitude};
      logData(componentName, secondsSinceOn(), data, 5);
    }
    else {
      // Indicate no fix with -1
      DATA_COMPONENT_READINGS[GPS_LATITUDE] = -1;
      DATA_COMPONENT_READINGS[GPS_LONGITUDE] = -1;
      DATA_COMPONENT_READINGS[GPS_HOUR] = -1;
      DATA_COMPONENT_READINGS[GPS_SPEED] = -1;
      DATA_COMPONENT_READINGS[GPS_ALTITUDE] = -1;
    }
  }
}


void logData(const char* componentName, float secondsSinceOn, float* data, int dataSize) {
  // Construct the initial part of the string to write
  String writeto = String(componentName) + "," + String(secondsSinceOn) + ",";
  // Open the file for appending
  logger.append(filename);
  // Write the initial part
  logger.print(writeto);
  // Iterate over the data array and append each value
  for (int i = 0; i < dataSize; i++) {
      logger.print(String(data[i]));  // Write data value
      if (i < dataSize - 1) {
        logger.print(",");  // Add comma if it's not the last element
      }
  }
  // End line after all data values are written
  logger.println();
  // Save changes
  logger.syncFile();
}

int getNumberOfPrevFlights() {
  int fileCount = 0;
  
  // Check if the file exists
  long sizeOfFile = logger.size("fileNum.txt");
  if (sizeOfFile > -1) {
    byte myBufferSize = 200; // Increase this buffer size to hold larger numbers
    byte myBuffer[myBufferSize];
    logger.read(myBuffer, myBufferSize, "fileNum.txt"); // Load myBuffer with contents of fileNum.txt
    
    String counterString = "";
    for (int x = 0 ; x < myBufferSize ; x++) {
      if (myBuffer[x] >= '0' && myBuffer[x] <= '9') {
        counterString += (char)myBuffer[x];
      }
    }
    fileCount = counterString.toInt();
    
  }
  // Increment the file count
  fileCount++;
  // Overwrite the file with the new file count
  logger.remove("fileNum.txt", false);
  logger.append("fileNum.txt"); 
  logger.print(String(fileCount));
  logger.syncFile(); // Ensure data is written to SD card

  return fileCount;
}


void collectDataFromBatteryMonitor() {
  unsigned long currentMillis = millis();
  if (currentMillis >= batteryTime + batteryTimer) {
    batteryTimer += batteryTime;

    DATA_COMPONENT_READINGS[BATTERY_PERCENT] = maxlipo.cellPercent();
    DATA_COMPONENT_READINGS[BATTERY_VOLTAGE] = maxlipo.cellVoltage();
    DATA_COMPONENT_READINGS[BATTERY_DISCHARGE_RATE] = maxlipo.chargeRate();

    const char* componentName = "BAT";
    float data[3];
    data[0] = DATA_COMPONENT_READINGS[BATTERY_PERCENT];
    data[1] = DATA_COMPONENT_READINGS[BATTERY_VOLTAGE];
    data[2] = DATA_COMPONENT_READINGS[BATTERY_DISCHARGE_RATE];
    logData(componentName, secondsSinceOn(), data, 3); 
    
  }
}

void printAllData() {
  Serial.println("--------------------------------------------------------");
  for (int i = 0; i < ENUM_SIZE; i++) {
    Serial.print(ENUM_NAMES[i]);
    Serial.print(": ");
    Serial.println(DATA_COMPONENT_READINGS[i]);
  }
}

void initBatteryMonitor(){
  if (!maxlipo.begin()) {
    ErrorLEDLoop("Couldn't find Adafruit MAX17048?\nMake sure a battery is plugged in!");
  }
  Serial.print(F("Found MAX17048"));
  Serial.print(F(" with Chip ID: 0x")); 
  Serial.println(maxlipo.getChipID(), HEX);
  
}



void transmitCurrentComponentReadings() {

  // Prepare a buffer to hold the transmitted message
  char radiopacket[256] = {0};  
    
  // Iterate through the DATA_COMPONENT_READINGS array and build the message
  char buffer[32];  // Temporary buffer for individual values

  for (int i = 0; i < ENUM_SIZE; i++) {
      // Format each floating-point value and store it in buffer
      snprintf(buffer, sizeof(buffer), "%.2f", DATA_COMPONENT_READINGS[i]);

      // Append the formatted value to radiopacket
      strncat(radiopacket, buffer, sizeof(radiopacket) - strlen(radiopacket) - 1);

      // If not the last element, append a comma
      if (i < ENUM_SIZE - 1) {
          strncat(radiopacket, ",", sizeof(radiopacket) - strlen(radiopacket) - 1);
      }
  }


    unsigned long currentMillis = millis();
    if (currentMillis >= rfTime + rfTimer) {
      rfTimer += rfTime;

      int state = radio.transmit((uint8_t *)radiopacket, strlen(radiopacket) + 1);  // +1 to include the null terminator

      if (state == RADIOLIB_ERR_NONE) {
        Serial.println("success!");
      } else {
        Serial.print("failed, error code: ");
        Serial.println(state);
      }
    }
}

void loop() {       

  collectDataFromBNO();  
  collectDataFromBME();  
  collectDataFromGPS();
  collectDataFromBatteryMonitor();
  transmitCurrentComponentReadings();   
}

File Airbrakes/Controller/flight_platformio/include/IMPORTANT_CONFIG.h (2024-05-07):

#pragma once

/* DEFINE FOR TARGET APOGEE OF ACE (IN METERS) */
#define ACE_TARGET_APOGEE 1295.4
#define ACE_SHUTOFF_THRESHOLD (ACE_TARGET_APOGEE-60) // Calibrate later if necessary

/* DEFINE FOR DEVELOPMENT MODE OF ACE (ENABLES DEBUG PRINTS AND SIMULATION) */
#define IS_DEVELOPMENT_MODE 1

/* DEFINE FOR STRICT INITIALIZATION CHECKS (REQUIRES FULL INIT TO BEGIN) */
#define CHECK_STRICT_INITIALIZATION 0

/* DEFINE FOR PERFORMING PHYSICAL SERVO ACTUATION TEST AT INIT */
#define DO_SERVO_ACTUATE_INIT_CHECK 1

/* DEFINE FOR DISABLING FAULT PROTECTION FOR TESTING PURPOSES*/
#define DISABLE_FAULT_PROTECTION 0

/* DEFINE FOR NUMER OF CYCLES OF AUTOMATIC EXTENSION UPON ENTERING CONTROL (0 is none)*/
#define FORCED_EXTENSION_CONTROL_CYCLES 0

/* DEFINE FOR STATUS LED */
#define ENABLE_STATUS_LED 0

/* DEFINE FOR INVERTING AIRBRAKES SERVO MOVEMENT*/
#define SERVO_INVERTED 1

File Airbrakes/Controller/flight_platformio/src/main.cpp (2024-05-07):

// Note: Important to keep order of includes correct to maintain consistent linking
// 1. External 3rd party library includes
// 2. Global definitions (may be used across our project)
// 3. Local includes
// 4. Local defines (used only in main.cpp)
// 5. Static variables


/* LIBRARY INCLUDES */
#include <Arduino.h>
#include <BasicLinearAlgebra.h>
#include <Wire.h>

/* GLOBAL DEFINES */
// Loop rates (Hz)
#define ONE_SEC_MICROS 1000000
#define SAMPLE_LOOP_FREQ 50 // Sample loop freq in Hz
#define KALMAN_LOOP_FREQ_PER_SAMPLES 1  // Compute per n=1 samples
#define CONTROL_LOOP_FREQ 20  // Control loop freq in Hz

/* LOCAL INCLUDES */
#include <Measurement.h>
// #include <accelReplace.h>  // Not using saturated IMU sim
#include <simulation.h>
#include <kalman.h>

#include <FlightMonitor.h>
#include <FSM.h>
#include <PID_Controller.h>
#include <AdafruitBMP388.h>
#include <AdafruitBNO085.h>
#include <AdafruitADXL345.h>
#include <SparkFunOpenLog.h>
#include <ServoMovement.h>

/**********************************************
 *** CHECK CONFIG CONSTANTS PRIOR TO LAUNCH ***
 **********************************************/
#include <IMPORTANT_CONFIG.h>
/**********************************************
 **********************************************/

/* LOCAL DEFINES */

/* STATIC VARIABLES */
// Delta timing variables
static unsigned long currentTime;
static unsigned long previousFilterReset;
static unsigned long previousSampleTime;
static unsigned int  previousComputeCounts; // counter for when compute should occur after n=1 samples
static unsigned long previousControlTime;

static const long sampleLoopMicros  = ONE_SEC_MICROS/SAMPLE_LOOP_FREQ;
// @note: DEPRECATED - compute loop is determined by counter instead of sample loop micros (previousComputeCounts)
// static const long computeLoopMicros = KALMAN_LOOP_FREQ_PER_SAMPLES * sampleLoopMicros;
static const long controlLoopMicros = ONE_SEC_MICROS/CONTROL_LOOP_FREQ;

// Flight monitor and sensor objects/variables
static AdafruitBMP388 alt_sensor;
static AdafruitBNO085 imu_sensor;
static AdafruitADXL345 acc_sensor;
static ServoMovement srvMovement;
static FlightMonitor fm_ace;
static FlightState currentState;
static bool measurementDataValid;
static Sample::Measurement currentMeasurement;  // Struct for holding current measurement

#if ENABLE_STATUS_LED
// Status LED pin
static int STATUS_LED_PIN = 9;
#endif

// Kalman filter external variables
extern BLA::Matrix<3> measuredAccel;
extern BLA::Matrix<3> inertialAccel;
extern BLA::Matrix<4> quaternions;

// PID controller object and global control
static PID_Controller pid(ACE_TARGET_APOGEE);
static double currentPIDControl = 0;

// OpenLog objects/variables
static SparkFunOpenLog logger;
static bool didWriteData = false;

// SDRAM configuration
#define RING_BUFFER_COLS 11
#ifdef RP2040_PLATFORM
  #warning "CONFIG: Configuring ringBuffer for RP2040 platform"
  #define RING_BUFFER_LENGTH 4000

  static float ringBuffer[RING_BUFFER_LENGTH][RING_BUFFER_COLS]; //contrains time,stateVec, and control value
#elif PORTENTA_H7_M7_PLATFORM
  #warning "CONFIG: Configuring ringBuffer for Portenta_H7 platform"
  #include <SDRAM.h>
  #define RING_BUFFER_LENGTH 30000

  static SDRAMClass ram;
  // float (*ringBuffer)[RING_BUFFER_LENGTH]; // Not currently using
  static float* SDRAM_base = (float*)0x60000000;  // Base pointer to DRAM start address
#endif
static int ringBufferIndex = 0;

// IMPORTANT CONFIG: Development debug variables
#if IS_DEVELOPMENT_MODE
// Debug variables
static int stateVecPrintCounter = 0;
static int counterSample = 0;
static float simSample[2] {0.0, 0.0};
#endif

// IMPORTANT CONFIG: Forced airbrakes actuation flight demonstration
#if FORCED_EXTENSION_CONTROL_CYCLES
static int numForcedExtensionControlCycles = FORCED_EXTENSION_CONTROL_CYCLES;
#endif


void setup() {
  int aceInitFails = 0;
  Serial.begin(38400);

#if IS_DEVELOPMENT_MODE
  while (!Serial) {
    ;  // wait for serial port to connect. Needed for native USB port only
  }


  Serial.println("> Initialized Serial comms!");
  Serial.println("\n\n\n\n\n\n\n");
  Serial.println("==== NOTE ====");
  Serial.println("THE ACE IS IN DEVELOPMENT MODE - PLEASE CONFIGURE FOR FLIGHT IN IMPORTANT_CONFIG.h");
  Serial.println("\n\n\n\n\n\n\n");
#endif
  
#ifdef PORTENTA_H7_M7_PLATFORM
  // Initialize SDRAM
  Serial.print("| Init SDRAM...");
  if (!ram.begin()) {
    ++aceInitFails;
    Serial.println("NOT OK!");
  } else {
    delay(100);
    Serial.println("OK!");
  }
#endif

  // Initialize FSM state
  Serial.print("| Init program state...");
  currentState = FlightState::detectLaunch;
  Serial.println("OK!");

  // Initialize sensor hardware
  if (!imu_sensor.init()) {
    ++aceInitFails;
  }
  if (!alt_sensor.init()) {
    ++aceInitFails;
  }
  if (!acc_sensor.init()) {
    ++aceInitFails;
  }
  

#if DO_SERVO_ACTUATE_INIT_CHECK
  Serial.println("> Notice: Performing servo actuation status check in 3 seconds...");

  int testState = 0;
  unsigned long servoInitCheckTime = micros();
  while (testState < 3) {

    currentTime = micros();
    if (currentTime >= servoInitCheckTime + 3000000) {
      servoInitCheckTime += 3000000;

      if (testState == 0) {
        Serial.print("> Extending to OPEN (SRV_MAX_EXTENSION_ANGLE): ");
        Serial.println(SRV_MAX_EXTENSION_ANGLE);
        srvMovement.setServoPosition(SRV_MAX_EXTENSION_ANGLE);
      }
      else if (testState == 1){
        Serial.println("> Retracting to CLOSE (stowAirbrakes)");
        srvMovement.stowAirbrakes();
      }
      testState++;
    }

    // Update srv as fast as possible for actuation test
    srvMovement.updateServoPosition();
    
  }
#endif

  // Initialize vectors/matrices
  Serial.print("| Init Kalman state...");
  if (!initializeKalmanFilter()) {
    ++aceInitFails;
    Serial.println("NOT OK!");
  } else {
    Serial.println("OK!");
  }

  // Initialize OpenLog
  if (!logger.init()) {
    ++aceInitFails;
  }

#if ENABLE_STATUS_LED
  // Initialize Status LED
  pinMode(STATUS_LED_PIN, OUTPUT);
#endif

  // ACE initialization summary status check
  if (!aceInitFails) {
    Serial.println("> Init ACE OK! Starting program...");
  } else {
    Serial.println("\n\n\n");
    Serial.print("WARNING: ACE did not initialize successfully! There were ");
    Serial.print(aceInitFails);
    Serial.println(" fails!");
    Serial.println("> Refer to above output to view failures...");
#if CHECK_STRICT_INITIALIZATION
    // Spin infinitely on failed init
    for ( ; ; ) {
      delay(5000);
      Serial.print("ACE INIT FAILED WITH ");
      Serial.print(aceInitFails);
      Serial.println(" ERRORS");
    } 
#endif
    Serial.println("\n\n\n!!! WARNING: ACE IS CONTINUING WITH FAILED INITIALIZATIONS !!!!\n");
  }
  delay(5000);

  // Update all delta timing timer variables with offset to REAL core loop start time
  previousComputeCounts = 0;
  previousFilterReset = micros();
  previousSampleTime = micros();
  previousControlTime = micros();
}
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

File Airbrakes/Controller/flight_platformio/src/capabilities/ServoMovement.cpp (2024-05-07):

#include <ServoMovement.h>
#include <IMPORTANT_CONFIG.h>

ServoMovement::ServoMovement(): targetAngle(0), lastAngle(0), distanceThreshold(1), 
previousServoUpdate(0), servoUpdateIntervalMicros(10 * 1000), numSteps(2)
{
  // Attach servo pin to D9 (PWM len min: 900 us, max: 2050us)  // this servo library is trolling us
  // Serial.print("| Init servo PWM...");
  srv.attach(9, SRV_MIN_PWM_LEN_MICROS, SRV_MAX_PWM_LEN_MICROS);

  // Default stow airbrakes on init
  #if SERVO_INVERTED
    targetAngle = SRV_MAX_EXTENSION_ANGLE + SRV_ANGLE_DEG_OFFSET;
  #else
    targetAngle = SRV_ANGLE_DEG_OFFSET;
  #endif
  srv.write(targetAngle);
  lastAngle = targetAngle;
}

ServoMovement::~ServoMovement()
{
}


// Function to initialize servo movement parameters
void ServoMovement::setServoPosition(int newTargetAngle) {
  #if SERVO_INVERTED
    targetAngle = SRV_MAX_EXTENSION_ANGLE - newTargetAngle;
  #else
    targetAngle = newTargetAngle;
  #endif
}

void ServoMovement::stowAirbrakes(){
  #if SERVO_INVERTED
    targetAngle = SRV_MAX_EXTENSION_ANGLE;
  #else
    targetAngle = SRV_ANGLE_DEG_OFFSET;
  #endif
}

void ServoMovement::updateServoPosition() {
  unsigned long currentMicros = micros();
  
  if (currentMicros >= previousServoUpdate + servoUpdateIntervalMicros) {
    previousServoUpdate += servoUpdateIntervalMicros;

    int virtLastAngle = lastAngle - SRV_ANGLE_DEG_OFFSET; // Last written angle, subtract offset for virtual angle

    // Serial.print("Last virtual angle: ");
    // Serial.println(virtLastAngle);
    // Serial.print("Target virtual angle: ");
    // Serial.println(targetAngle);

    if (abs(targetAngle - virtLastAngle) > distanceThreshold) { // Only move if there is a significant difference
      int stepAngle = (targetAngle - virtLastAngle) / numSteps; // Determine virtual step size
      int writeAngle = lastAngle + stepAngle;  // Actual angle with offset
      if (writeAngle >= SRV_ANGLE_DEG_OFFSET && writeAngle <= SRV_MAX_EXTENSION_ANGLE + SRV_ANGLE_DEG_OFFSET) {
        // Serial.print("Writing to actual angle: ");
        // Serial.println(writeAngle);
        srv.write(writeAngle);
        lastAngle = writeAngle;
      }
    }
  }
}

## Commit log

2023-10-02 Re-Merge dev/payload Main.ino milestone (#40)
    * Create GPS_TEST.ino
    * Create IMU_TEST.ino
    * Create RP2040_TEST.ino
    * Create RF_TEST.ino
    * Create BME680_TEST.ino
    * Create BATTERY_TEST.ino
    * Create LOGGING_TEST.ino
    * Added code for BME680_TEST.ino
    * IMU test code
    * test2
    * Battery test
    * adding empty main
    * still strying
    * GPS Test File
    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
    [BATTERY_TEST.ino, BME680_TEST.ino, BME680_TEST2 .ino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]
2023-10-02 dev/airbrakes outline ACE FSW (#41)
    * init Airbrakes folder
    * Added data and barebones simulation
    * Update README.md
    * LaunchAndControlSim
    * update controller with drag VLT and integral term
    * change errorDecay to be dependent on altitude
    * update errorDecayFunc
    * update VLT
    * clean-up
    * Update LaunchAndControlSim.ipynb
    * Update LaunchAndControlSim.ipynb
    * Update LaunchAndControlSim.ipynb
    * Add Kalman Filter
    * Add process noise
    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
    [ACE.brd, ACE.sch, Adafruit_BNO08x.brd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]
2024-01-14 Update pio-build.yml
    Yet another update to better filter paths + payload name change
2024-05-07 Merge dev/airbrakes to 2023-2024 Electrical (#106)
    added random process noise, this should be fixed
    * Improve Process Noise
    * Fix Plots
    * fix comment
    * Refine
    * Change some numbers around
    * Update integrato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
    [ACE.brd, ACE.sch, ALT.csv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]
2024-05-07 Merge dev/payload to 2023-2024 Electrical (#107)
    * trying
    * Put IMU test in its own folder
    * Correct IMU test code
    * added logger test
    * Update main.ino
    * Update main.ino
    * new enum
    * Update main.ino
    * Update main.ino
    * fixing main code
    * Remove trailing merge conflict tag
    * Openlogging overhaul, transmit code created, battery monit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
    [PCE_Trace_Power_test.brd, PCE_Trace_Power_test.sch]
2024-05-07 Merge dev/avionics to 2023-2024 Electrical (#105)
    * Move commits to dev/avionics
    * :O
    * Abby test
    * abbys files
    * Update detach_arm_transmission_copy_20240321230634.ino
    * Update and rename Avionics/detach_arm_transmission_copy_20240321230634/detach_arm_transmission_copy_20240321230634.ino to Avionics/Quadcopter_Base_Station.ino
    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
    [pyvenv.cfg]

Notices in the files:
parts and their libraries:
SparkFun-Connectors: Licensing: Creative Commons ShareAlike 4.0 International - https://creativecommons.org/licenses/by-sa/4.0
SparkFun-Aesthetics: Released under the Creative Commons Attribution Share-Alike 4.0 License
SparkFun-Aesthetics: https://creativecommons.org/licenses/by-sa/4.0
